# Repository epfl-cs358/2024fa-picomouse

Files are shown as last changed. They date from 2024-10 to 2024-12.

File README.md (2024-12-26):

# Picomouse

## Description
 
This project aims to create from scratch a micromouse and be able to run it on a 10x10 maze. The design of the mouse, the choice of components, the implementation of the code and the construction of the maze are parts of the project. Our team was responsible of the walls and pillars and another team had to construct the floor. The purpose of this project is to discover how to combine hardware and software and to learn how to work in a team of 6 persons.

## Table of Contents
1. [Description](#description)
2. [Mouse Components](#mouse-components)
3. [Mouse Preparation](#mouse-preparation)
4. [Mouse Assembly](#assembling-the-mouse)
5. [Maze](#maze)
6. [Software Overview](#software-overview)
7. [Software Installation](#software-installation)
8. [Sensors calibration](#sensors-calibration)
9. [Distance calculation](#distance-calculation)
10. [Computation distances with encoders](#computation-distances-with-encoders)
11. [What does the mouse?](#what-does-the-mouse)
12. [Improvements](#improvements)

## Mouse Components:
- 2 x N20 600rpm dc brushed motors
- MX1508 motor driver
- 9 volt battery
- ESP-32-vroom 32
- 5 x DFROBOT SEN0427 TOF
- DFRobot Gravity I2C BMI160 Gyroscope
- Small Bead
- M2 screws and bolts 

## Mouse Preparation:
 ### 3d Printing the components:
  The 3d files are in the CAD folder. \
  We used 10% infill for the printing. \
  1.Print the base plate: 
  
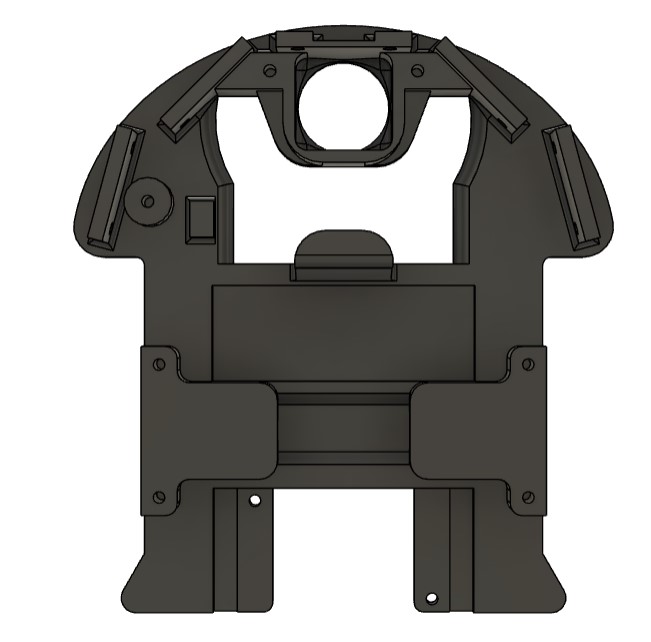
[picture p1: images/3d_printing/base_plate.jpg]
Base Plate
  
  
  2.Print the motors holders: 
  
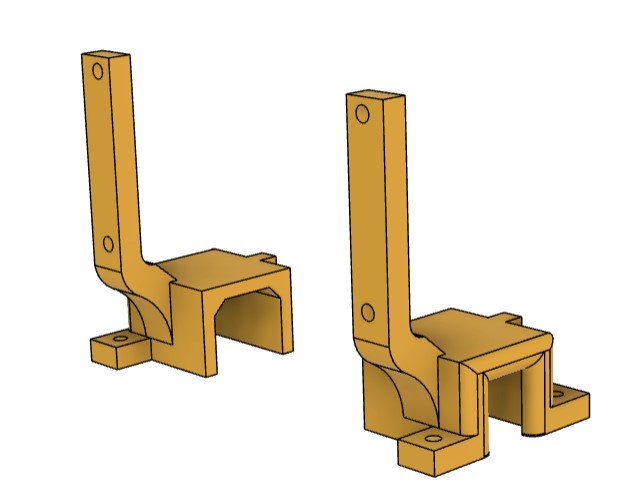
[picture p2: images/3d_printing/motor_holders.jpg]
Motor holder
   
  
  3.Print the bead holder (cap): 
  
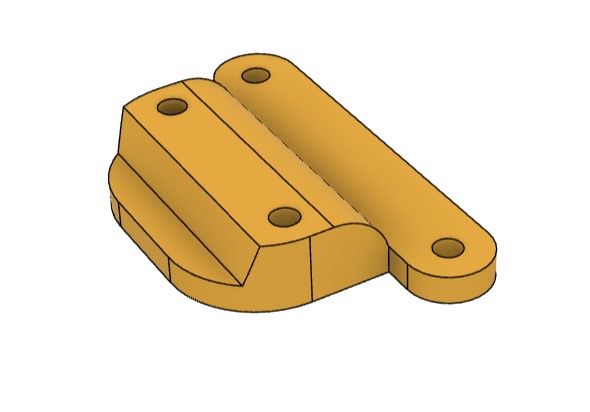
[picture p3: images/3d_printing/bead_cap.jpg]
Bead cap
   
  
  4.Print the weels: 
  The weels are composed of 2 parts: 
  - The inner wheel support printed in hard plastic (PETG/PLA). 
  - Our rubber is printed with ninjaflex TPU but elastic rubber can also be used.

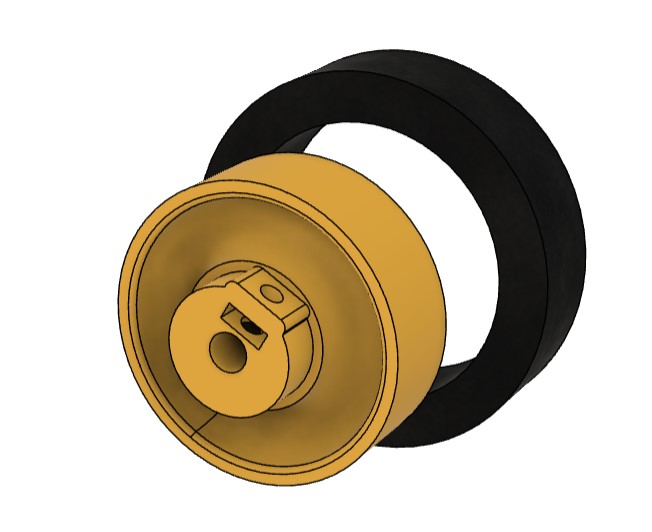
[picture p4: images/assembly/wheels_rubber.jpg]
wheels
  

## Assembling the Mouse:
  The whole mouse can be build with bolts and screws but threaded insert can be used to disassemble the mouse easily.

  #### 1.Assemble the wheels:
  Glue the rubber on the wheel. \
  Place a M2 hexnut in the dedicated slot.
  
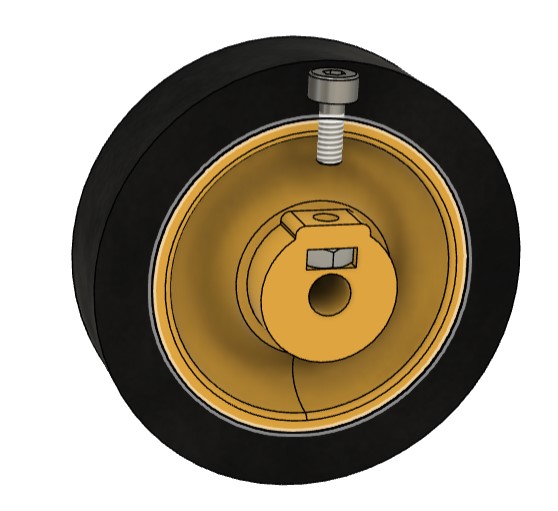
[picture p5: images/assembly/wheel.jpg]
wheels_rubber
  

  #### 2.Place and screw the buck convertor: 
    
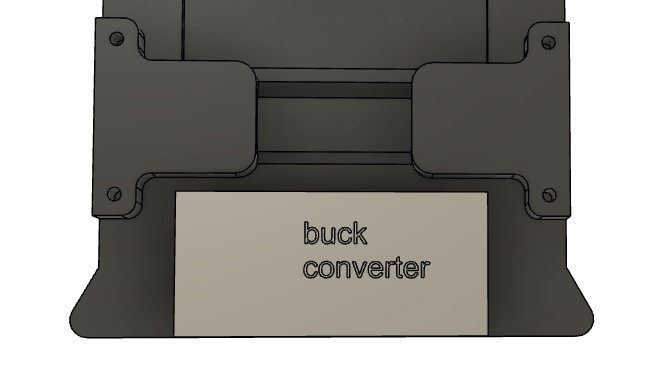
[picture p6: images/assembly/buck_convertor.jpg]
Buck convertor
   

 #### 3.Place the motors and fix them with the motors holder: 
   
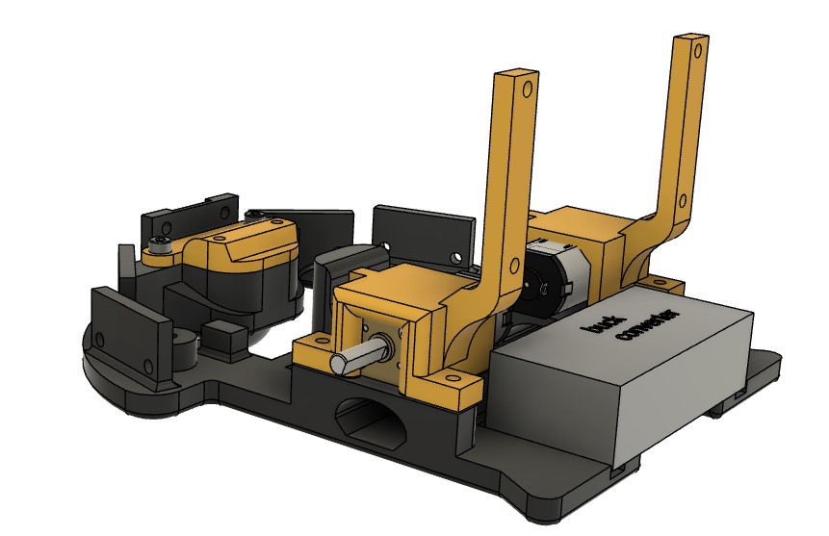
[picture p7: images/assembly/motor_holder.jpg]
Motor holder
   

 #### 4.Assemble the weels and fix them to the motor axis:

 #### 5.Place the battery: 
 
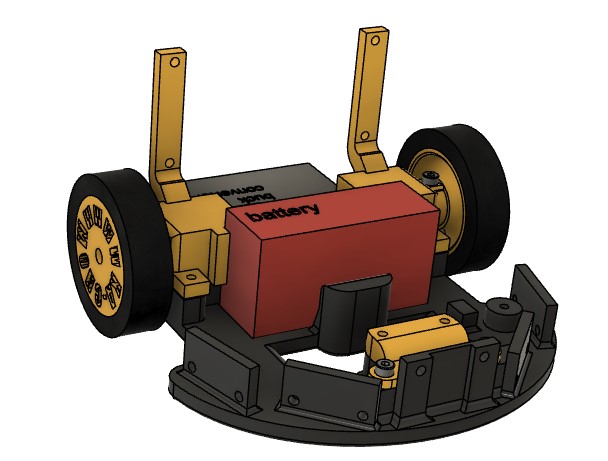
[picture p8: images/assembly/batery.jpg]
Batery
   

 #### 6.Place and screw the TOF's sensors to their dedicated slot: 
   
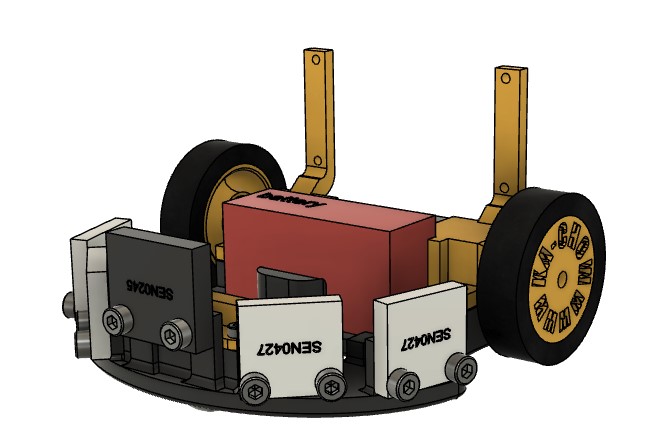
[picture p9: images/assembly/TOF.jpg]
TOF
   

 #### 7.Place and screw the gyroscope: 
  
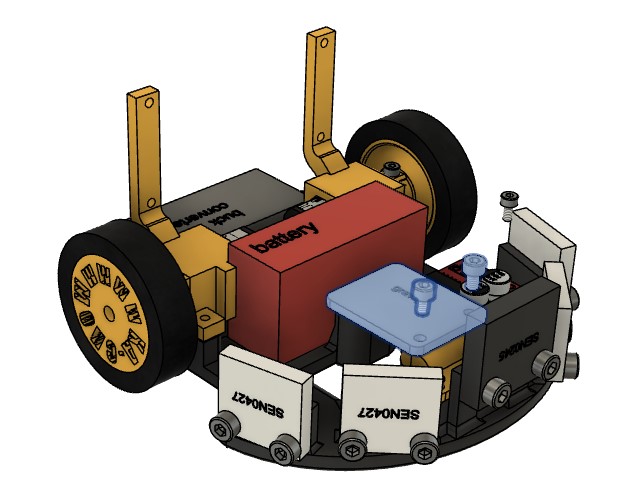
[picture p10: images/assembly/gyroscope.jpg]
   
  
  #### 8.Place and screw the ESP-32 to the back of the motor holder: 
  
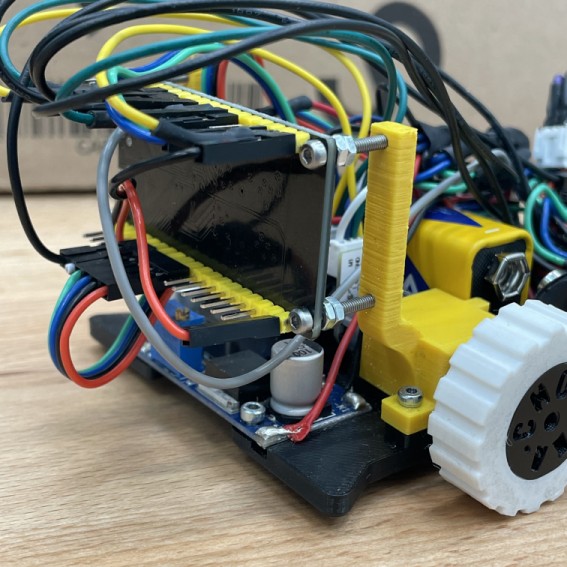
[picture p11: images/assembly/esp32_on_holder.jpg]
   
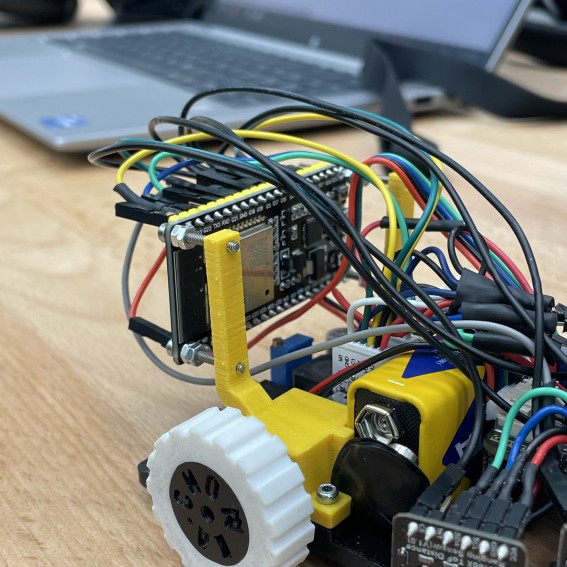
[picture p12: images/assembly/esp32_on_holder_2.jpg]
  

  ### Wiring:
  

## Maze
The competition maze is made by 18cm x 18cm cells with 2cm width walls and 16 cm x 16 cm space inside the cells.
There is also an other maze design that uses 17cm x 17cm cells with 1cm width walls. \
We decided to make the first option to align with the competition design however the second option uses less platic and wood. \
We had the constraint to make a maze that is easily dissmountable thus we used Scratch to attach the walls and the pillars to a carpet. 

### Walls:
Option1. We used 6mm and 8mm thick mdf plates. \
    See the CAD for the dimension of the cut, we used a C02 laser cutter. \
    The wall is composed of 2 plates of 16cm x 5cm and 2 dowel of 2.5cm x 4.5cm that need to be glued together. 

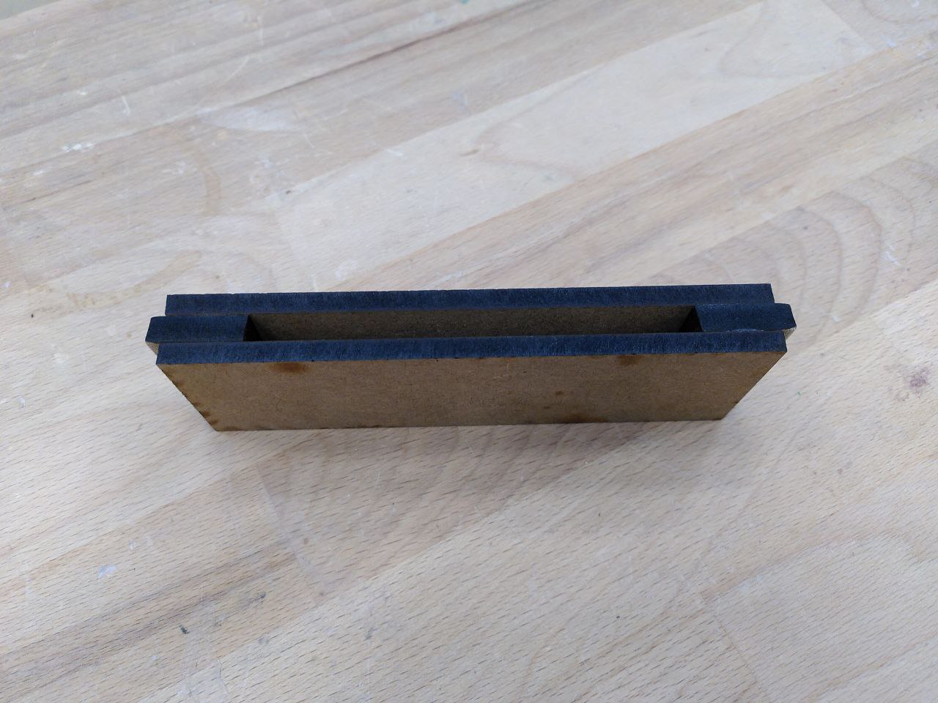
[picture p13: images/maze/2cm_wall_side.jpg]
walls2cm
 

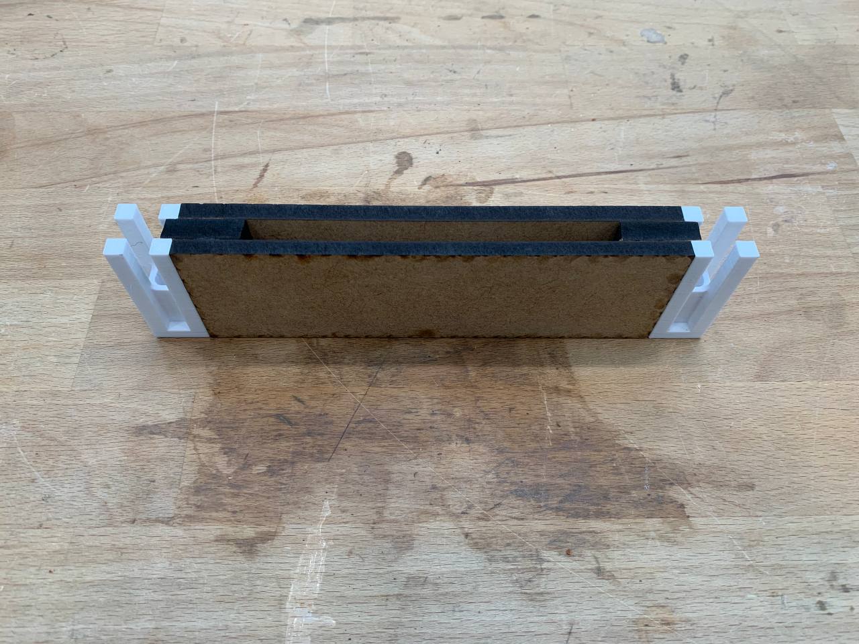
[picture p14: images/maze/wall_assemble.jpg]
walls2
     

Option2. Same as option 1 but with 3mm and 4mm thick mdf plates. \
We get the following wall:

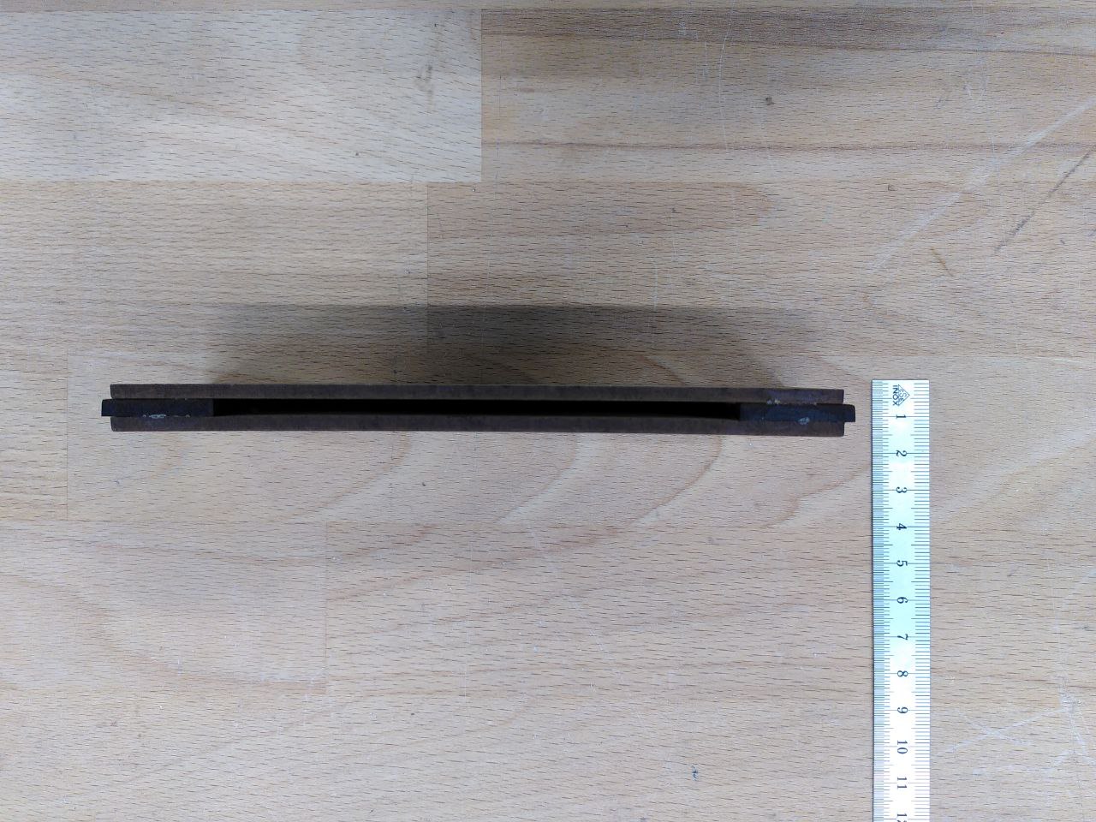
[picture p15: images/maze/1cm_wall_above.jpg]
wall1cm
 

### Pillars:
Option1. 3d print the 2cm x 2cm x 5cm pillars \

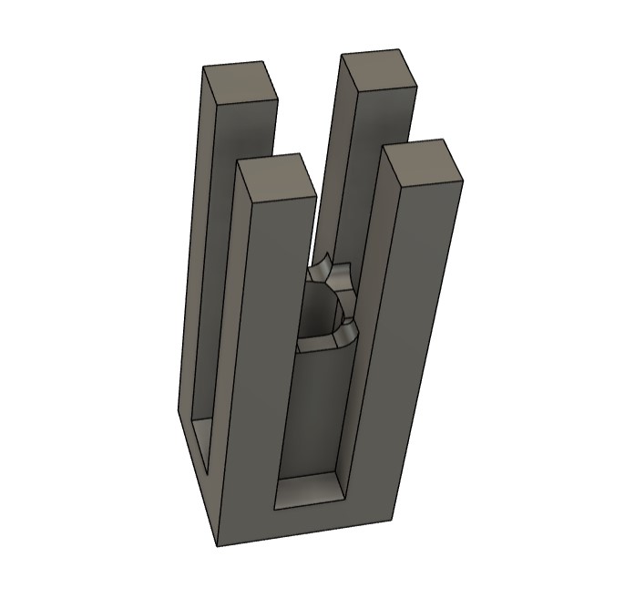
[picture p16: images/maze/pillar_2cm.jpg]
pillar_2
 

Option2. 3d print the 1cm x 1cm x 5cm pillars \

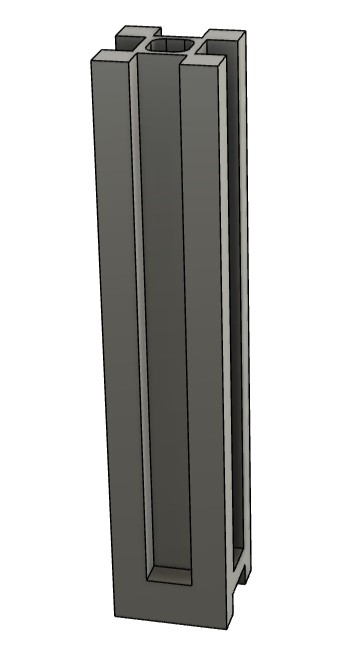
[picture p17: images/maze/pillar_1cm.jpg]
pillar_1
 
    
Both of them have an option to add a M2 hexnut inside so the pillars can be screwed underneath.\
The bolt can easily be placed using a screwdriver by pushing the bolt until you hear a pop for the 2cm x 2cm pillar. \
For the 1cm x 1cm pillar the bolt has to be glued underneath. \
The bolt should be locked in place. 

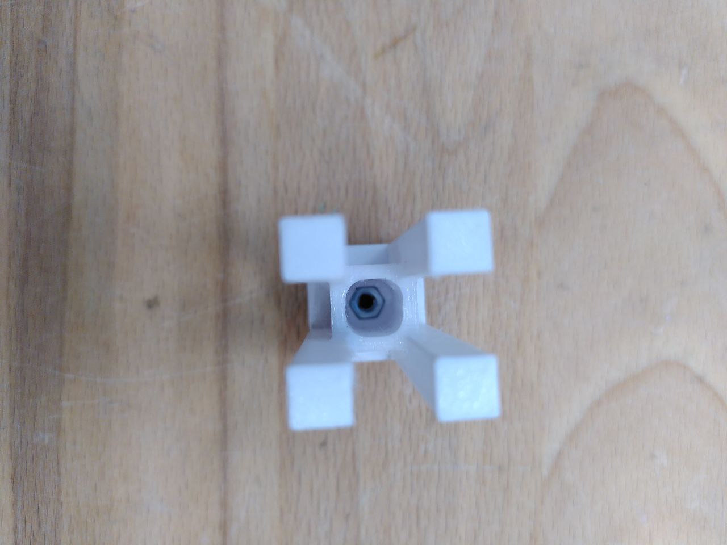
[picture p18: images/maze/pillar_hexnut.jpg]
pillar_hexnut
 

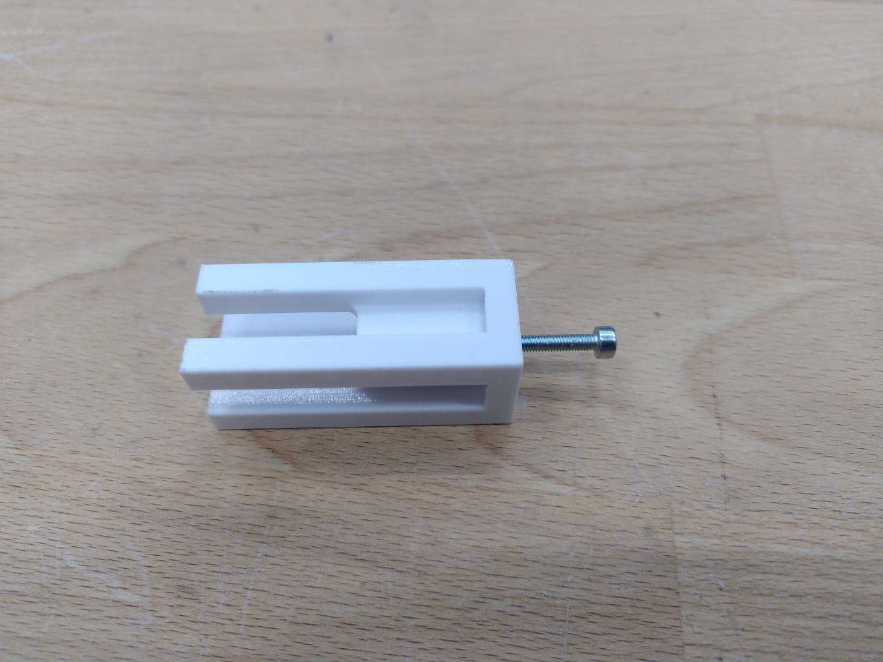
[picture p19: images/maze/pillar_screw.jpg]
pillar_screw
 

## Software Overview
### Code interface
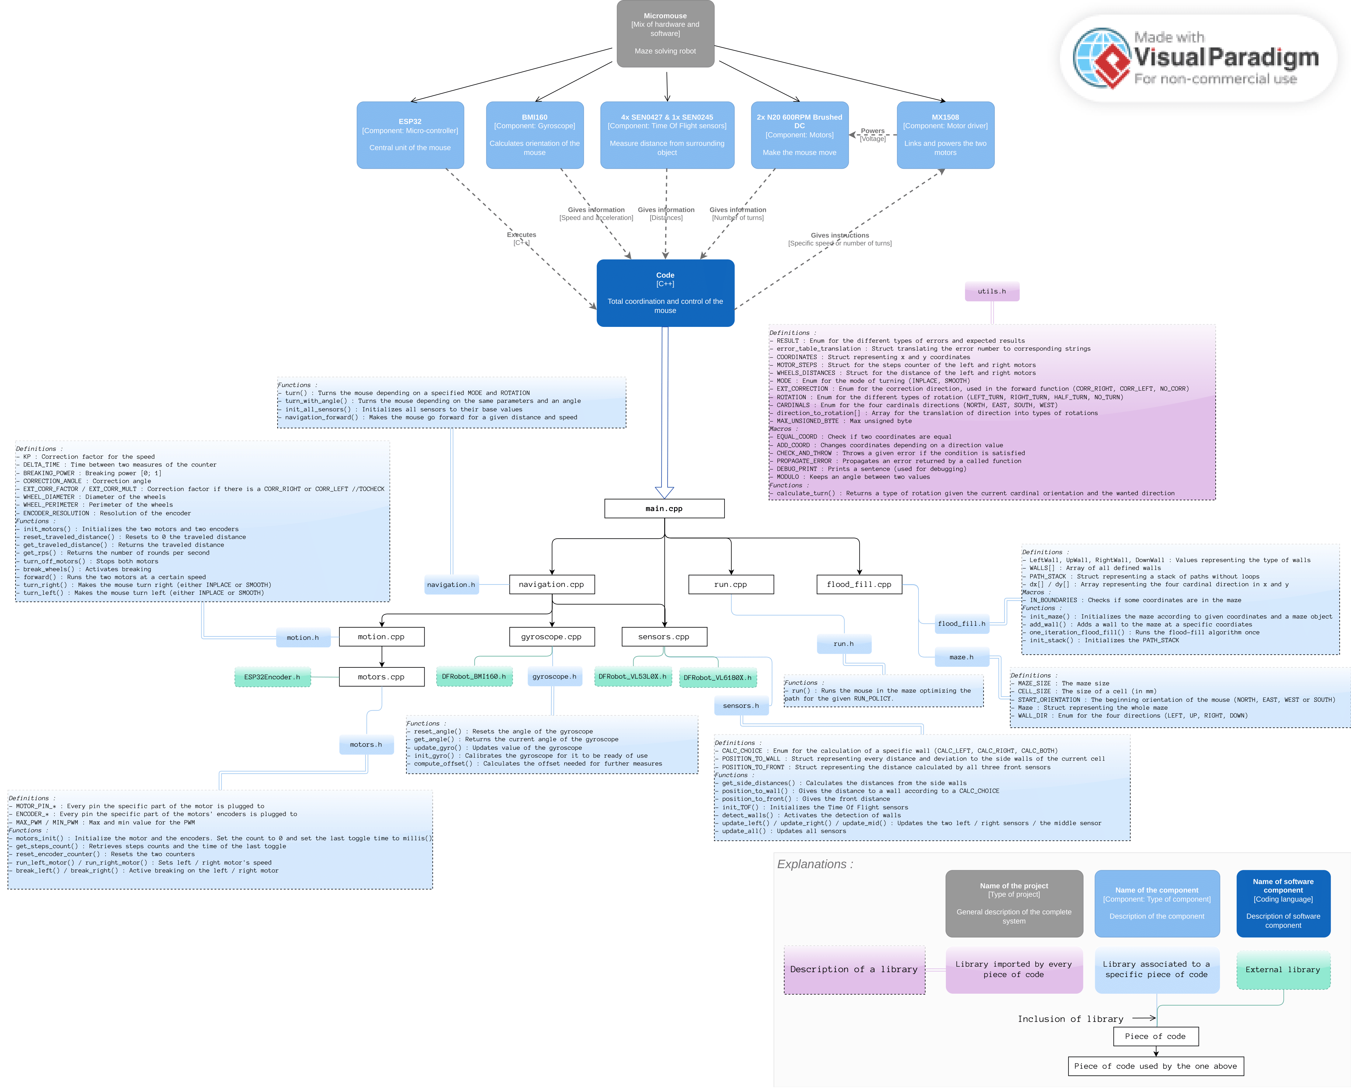
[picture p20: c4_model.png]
here
You can find a detailed scheme representing the relations of all components and pieces of code  (in .png) and here (in .pdf).
## Software Installation
  ### Software Prerequisites:
  
  - Arduino IDE
  - Python 3.10
  - Python libraries: (bleak, pygame)

### Installation:

1. Clone the repository to your local machine:
   ```bash
   git clone https://github.com/epfl-cs358/2024fa-picomouse.git
   cd 2024fa-picomouse
   ```

## Sensors calibration:
  ### TOF calibration:
  The Tof sensors need to be calibrated individually, to do that we measured different distances for each sensors and did a linear regression on the measurement     given the actual distance. \
  For our sensors we get the following graphs: \
  Where the x axis denotes the real distance and the y axis denotes the measured value. \
  The green line represent the expected slope, and the black line represent the measurements. 

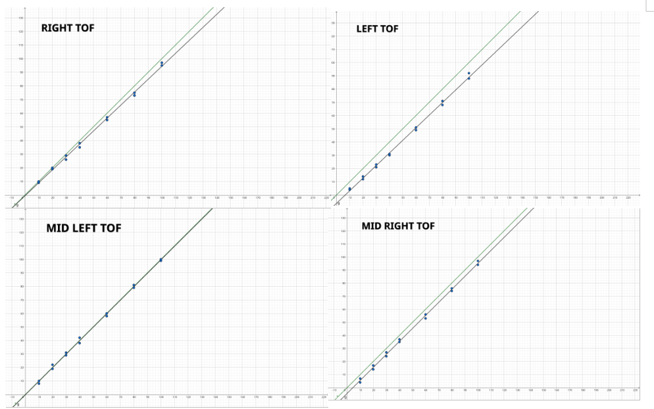
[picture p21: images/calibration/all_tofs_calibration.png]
all TOFs
  

  We get 5 slopes: \
  Left_y = 0.951x - 6.273 \
  Mid_Left_y = 0.998x - 0.189 \
  Mid_y = 1.000x - 0.000\
  Mid_Right_y = 0.995x - 4.407 \
  Right_y = 0.958x - 1.176 

  The values you will get need to be changed in sensors.h, the SLOPE and OFFSET of each captors. 

  ### Gyroscope calibration:
   The bmi60 chip is knowned for it's natural drift. To counter that the mouse, at initialization, \
   read's CALIBRATION_OFFSET_NB_ITERATIONS times the gyroscope and average the values to obtain the offset.\
   The offset itself is not sufficient, we also calibrated it with an affine function.\
   The gyroscope is also measured GYRO_NB_ITERATIONS times and average it out to mitigate the noise. \
   This parameter can also be changed in gyroscope.h. \
   If required, you can add and activation threshold.

### Distance Calculation:
Using the TOF sensors we can estimate the mouse position to a left or right wall.
We can get the mouse orientation and its distance to the wall (from the center of the mouse).
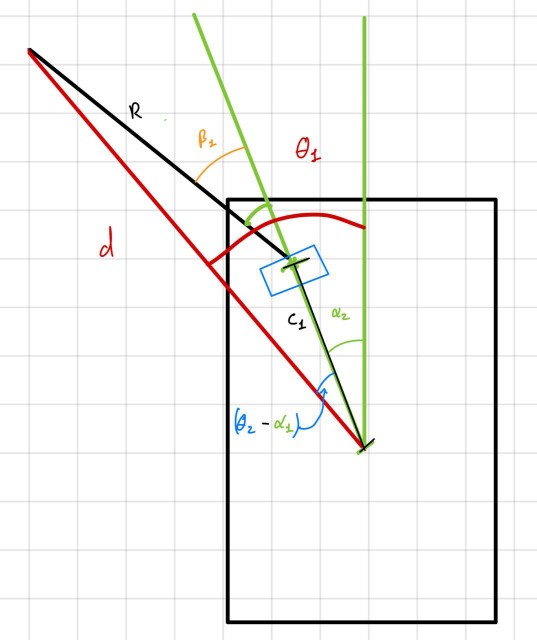
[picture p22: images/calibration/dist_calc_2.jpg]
trigo_1


$$
    \begin{aligned}
    \text{Given: } \ & \alpha_1 , \ c_1 , \ \beta_1, \ r \\
    \text{To be found: } \ & d, \ \theta_1 \\
    \newline
    d &= \sqrt{r^2 + c_1^2 - 2 \cdot r \cdot c_1 \cdot \cos(\pi - \beta_1)} \\
    \theta_1 &= \alpha_1 + \arccos\left(\frac{d^2 + c_1^2 - r^2}{2 \cdot d \cdot c_1}\right) \\
    \end{aligned}
$$

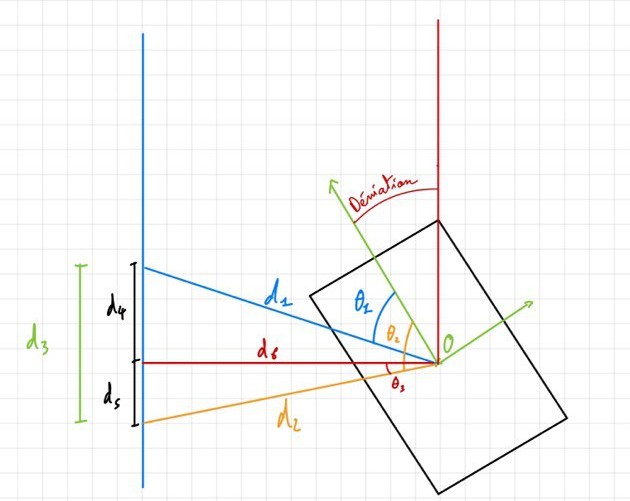
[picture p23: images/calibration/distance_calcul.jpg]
trigo_2


$$
    \begin{aligned}
    \text{Given: } \ & d_1, \ \theta_1, \ d_2, \ \theta_2 \\
    \text{To be found: } \ & d_3, \ d_5, \ d_6 \\
    \newline
    d_3 &= \sqrt{d_1^2 + d_2^2 - 2 \cdot d_1 \cdot d_2 \cdot \cos(\theta_1 - \theta_2)} \\
    d_5 &= \frac{d_2^2 + d_3^2 - d_1^2}{2 \cdot d_3} \\
    d_6 &= \sqrt{d_2^2 - d_5^2} \\
    \end{aligned}
$$

If you change the sensors disposition you need to changes those values in sensors.cpp.

## Computation distances with encoders
To compute the travel distance, one needs to know the real perimeter of the wheels and the number of pulsations transmitted by the encoder during one wheel revolution. To do that, you can modify in motion.h the constant WHEEL_DIAMETER and ENCODER_RESOLUTION.\
To compute the encoder's resolution, print get_steps_count() in a while loop and turn manually the wheel to measure the number of steps needed for one revolution.

## UI
The UI made for monitoring the mouse's position and state of the maze stored in the micro-controller is written in Python, using the [Pygame Community Edition library](https://github.com/pygame-community/pygame-ce). 
To use the provided code, you'll need to install pygame-ce (``pip install pygame-ce``) which should already be done if you installed the requirements.

### How to use
If you are simply trying to visualize the maze and play with it offline, you'll have to understand how it is interpreted by the code. Every cell is represented by a set of 4 bits. Each of these bits represents a wall. In order, the first bit represents the left wall, the second, the upper wall, the third, the right wall, the fourth, the bottom wall (i.e. 0b1010 represents a cell with a wall on the left and wall on the right).
#### Example of a complete maze
```
maze = [[0b0000, 0b0101, 0b0110, 0b1000, 0b0000, 0b0000, 0b0000, 0b0000],
        [0b1010, 0b1111, 0b1011, 0b1000, 0b0000, 0b0001, 0b0000, 0b0000],
        [0b1001, 0b0110, 0b1101, 0b0000, 0b0011, 0b1110, 0b1001, 0b0000],
        [0b0110, 0b1001, 0b0110, 0b1011, 0b1110, 0b1010, 0b1111, 0b1000],
        [0b0000, 0b0110, 0b1001, 0b0101, 0b0001, 0b0010, 0b1101, 0b0000],
        [0b0000, 0b0000, 0b0100, 0b0100, 0b0110, 0b1001, 0b0110, 0b0000],
        [0b0000, 0b0000, 0b0000, 0b0000, 0b0000, 0b0100, 0b0000, 0b0000],
        [0b0000, 0b0000, 0b0000, 0b0000, 0b0000, 0b0000, 0b0000, 0b0000]]
```
This represents the following maze :
Example UI Maze

## What does the mouse?:
The mouse navigate through the maze with the support of the gyroscope and the sensors. She does 3 runs : one to search the target cell (corner of the maze in diagonal of the start cell) by stopping in each cell, one to search a second path that could be faster than the first one when returning to the start cell, and one to run through the maze with the best path and without stopping at each cell. We use the gyroscope to keep track of and correct the current angle of the mouse in the global space. The sensors were used to detect the walls at the sides and in front of the mouse, and to recalibrate her when facing a wall.

## Improvements:
  1. Reduce the BLE (bluetooth) library so it can be compiled on the esp and used for the python script.
  2. Use a PCB as the mouse base plate to reduce the weight of the plastic plate and the cable.
  3. Make smooth turns when running the maze (after the exploration phase).
  4. Redesign of the mouse: bring closer the center of rotation to the sensors to make in place turns in less space.
  5. Better error handling for imperfect maze.
  6. Implementation of PID algorithm for sensors. The gyroscope has some limits in the precision of the turns and in straight lines, inclusion of the sensors in         the process would improve the general navigation.
  7. Ligthen weight of the mouse with a LiPo and a smaller buck converter.
  8. Usage of buck converter on motors to run at constant 6V.
  9. Redesign the floor of the maze to be more consistent (especially for the walls).
  10. Reduce the use of floating point calculations in the code using "scaled" fixed point values to improve calculation speed.

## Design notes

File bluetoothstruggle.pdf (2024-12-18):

Bluetooth struggle

This document explains why we could not finalise the UI for our project.

As part of our project, we developed a python UI which allowed us to visualise they movements of the micromouse inside the maze. The UI was implemented with Pygame, and data from micromouse was transmitted using bluetooth. For this we used the BLE library, which worked, however the big issue was the large size of the BLE library, which took around 80% of space in our ESP32. This was not usable, as the code for micromouse could not fit in the remaining 20%. We thus went on a quest to find an alternative solution. Main idea was to use a lighter bluetooth library, notably the bluetoothSerial.h, but this presented the issue of receiving the data within the pygame code.

First approach was to try to pair the esp32 with a computer directly. This did not work on Windows, we did manage to setup a bluetooth serial terminal, but we did not manage to transfer the results into the python script. Next we tried on linux, setting up the connection manually with bluetoothctl, then using command line pipelines to get the data to the python, but this approach also failed as we could not setup the bluetooth communication well.

Next idea was to use a raspberry pi. This is because raspberry pi allows you to control the GPIO pins with a python script instead of a C code like in arduino or ESP, and so we planned to import pygame in that same script and use the UI that way. We tried this by hooking up a hc05 bluetooth sensor directly to the GPIO pins of raspberry pi, but soon discovered that since raspberry has bluetooth built in, like a computer, there was not any good support for external bluetooth module. Using the built in raspberry bluetooth would be equivalent to what we tried on linux machine, so we did not attempt that. Instead we jumped through yet another loop, connecting the hc05 to arduino, arduino with a cable to raspberry, where the python code would manage the serial connection to receive bluetooth data and the pygame UI.
Picture of connection:
HC05 is connected based on the wiring to arduino, with voltage divider on its rx pin as it only accepts 3.3v logic. USB cable connects the arduino to raspbery.

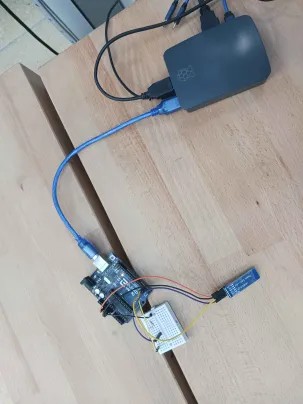
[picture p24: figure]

This finally worked. We were receiving bluetooth data sent from phone, and we had pygame running in the same script:

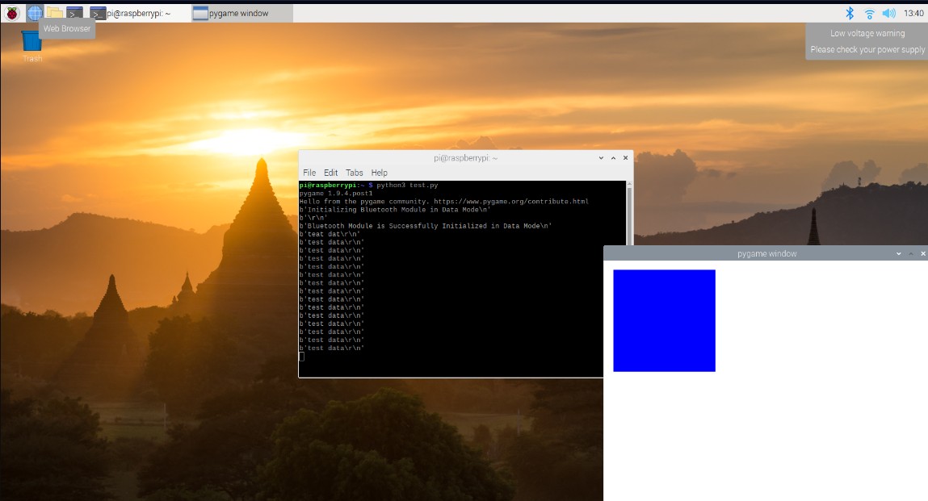
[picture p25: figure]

Code for the arduino and raspberry is also uploaded on github.
However, we ran into a last issue. Pairing the HC05 from arduino and ESP32 in micromouse ended up being more difficult than expected, and we did not manage to solve this in time to present UI in our final version of project. However we still spent a lot of time on this, and so I believe that having this document explaining the work is important.

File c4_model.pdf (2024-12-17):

### Micromouse [Mix of hardware and software]

### Maze solving robot

### ESP32 [Component: Micro-controller]

### Central unit of the mouse

### BMI160 [Component: Gyroscope]

### Calculates orientation of the mouse

### 4x SEN0427 & 1x SEN0245 [Component: Time Of Flight sensors]

### Measure distance from surrounding object

### 2x N20 600RPM Brushed

DC

### [Component: Motors]

### Make the mouse move

### Code

[C++]

### Total coordination and control of the mouse

Executes
[C++]

Gives information
[Speed and acceleration]

Gives information
[Distances]

Gives information
[Number of turns]

Gives instructions
[Specific speed or number of turns]

### main.cpp

MX1508

### [Component: Motor driver]

### Links and powers the two motors

Powers
[Voltage]

### flood_fill.cpp

flood_fill.h

Definitions :
- LeftWall, UpWall, RightWall, DownWall : Values representing the type of walls
- WALLS[] : Array of all defined walls
- PATH_STACK : Struct representing a stack of paths without loops
- dx[] / dy[] : Array representing the four cardinal direction in x and y Macros :
- IN_BOUNDARIES : Checks if some coordinates are in the maze
Functions :
- init_maze() : Initializes the maze according to given coordinates and a maze object
- add_wall() : Adds a wall to the maze at a specific coordiates
- one_iteration_flood_fill() : Runs the flood-fill algorithm once
- init_stack() : Initializes the PATH_STACK gyroscope.cpp

gyroscope.h

Functions :
- reset_angle() : Resets the angle of the gyroscope
- get_angle() : Returns the current angle of the gyroscope
- update_gyro() : Updates value of the gyroscope
- init_gyro() : Calibrates the gyroscope for it to be ready of use
- compute_offset() : Calculates the offset needed for further measures

maze.h

Definitions :
- MAZE_SIZE : The maze size
- CELL_SIZE : The size of a cell (in mm)
- START_ORIENTATION : The beginning orientation of the mouse (NORTH, EAST, WEST or SOUTH)
- Maze : Struct representing the whole maze
- WALL_DIR : Enum for the four directions (LEFT, UP, RIGHT, DOWN)
motion.h | motion.cpp

Definitions :
- KP : Correction factor for the speed
- DELTA_TIME : Time between two measures of the counter
- BREAKING_POWER : Breaking power [0; 1]
- CORRECTION_ANGLE : Correction angle
- EXT_CORR_FACTOR / EXT_CORR_MULT : Correction factor if there is a CORR_RIGHT or CORR_LEFT //TOCHECK
- WHEEL_DIAMETER : Diameter of the wheels
- WHEEL_PERIMETER : Perimeter of the wheels
- ENCODER_RESOLUTION : Resolution of the encoder
Functions :
- init_motors() : Initializes the two motors and two encoders
- reset_traveled_distance() : Resets to 0 the traveled distance
- get_traveled_distance() : Returns the traveled distance
- get_rps() : Returns the number of rounds per second
- turn_off_motors() : Stops both motors
- break_wheels() : Activates breaking
- forward() : Runs the two motors at a certain speed
- turn_right() : Makes the mouse turn right (either INPLACE or SMOOTH)
- turn_left() : Makes the mouse turn left (either INPLACE or SMOOTH)

### motors.cpp

motors.h

Definitions :
- MOTOR_PIN_* : Every pin the specific part of the motor is plugged to
- ENCODER_* : Every pin the specific part of the motors' encoders is plugged to
- MAX_PWM / MIN_PWM : Max and min value for the PWM
Functions :
- motors_init() : Initialize the motor and the encoders. Set the count to 0 and set the last toggle time to millis()
- get_steps_count() : Retrieves steps counts and the time of the last toggle
- reset_encoder_counter() : Resets the two counters
- run_left_motor() / run_right_motor() : Sets left / right motor's speed
- break_left() / break_right() : Active breaking on the left / right motor
navigation.h | navigation.cpp

Functions :
- turn() : Turns the mouse depending on a specified MODE and ROTATION
- turn_with_angle() : Turns the mouse depending on the same parameters and an angle
- init_all_sensors() : Initializes all sensors to their base values
- navigation_forward() : Makes the mouse go forward for a given distance and speed

### sensors.cpp

sensors.h

Definitions :
- CALC_CHOICE : Enum for the calculation of a specific wall (CALC_LEFT, CALC_RIGHT, CALC_BOTH)
- POSITION_TO_WALL : Struct representing every distance and deviation to the side walls of the current cell
- POSITION_TO_FRONT : Struct representing the distance calculated by all three front sensors
Functions :
- get_side_distances() : Calculates the distances from the side walls
- position_to_wall() : Gives the distance to a wall according to a CALC_CHOICE
- position_to_front() : Gives the front distance
- init_TOF() : Initializes the Time Of Flight sensors
- detect_walls() : Activates the detection of walls
- update_left() / update_right() / update_mid() : Updates the two left / right sensors / the middle sensor
- update_all() : Updates all sensors

utils.h

Definitions :
- RESULT : Enum for the different types of errors and expected results
- error_table_translation : Struct translating the error number to corresponding strings
- COORDINATES : Struct representing x and y coordinates
- MOTOR_STEPS : Struct for the steps counter of the left and right motors
- WHEELS_DISTANCES : Struct for the distance of the left and right motors
- MODE : Enum for the mode of turning (INPLACE, SMOOTH)
- EXT_CORRECTION : Enum for the correction direction, used in the forward function (CORR_RIGHT, CORR_LEFT, NO_CORR)
- ROTATION : Enum for the different types of rotation (LEFT_TURN, RIGHT_TURN, HALF_TURN, NO_TURN)
- CARDINALS : Enum for the four cardinals directions (NORTH, EAST, SOUTH, WEST)
- direction_to_rotation[] : Array for the translation of direction into types of rotations
- MAX_UNSIGNED_BYTE : Max unsigned byte
Macros :
- EQUAL_COORD : Check if two coordinates are equal
- ADD_COORD : Changes coordinates depending on a direction value
- CHECK_AND_THROW : Throws a given error if the condition is satisfied
- PROPAGATE_ERROR : Propagates an error returned by a called function
- DEBUG_PRINT : Prints a sentence (used for debugging)
- MODULO : Keeps an angle between two values
Functions :
- calculate_turn() : Returns a type of rotation given the current cardinal orientation and the wanted direction
DFRobot_BMI160.h | DFRobot_VL53L0X.h | DFRobot_VL6180X.h

### Library imported by every piece of code

### Library associated to a specific piece of code

### External library

ESP32Encoder.h

### Name of the project [Type of project]

### General description of the complete system

### Name of the component [Component: Type of component]

### Description of the component

### Name of software component [Coding language]

### Description of software component

### Piece of code

## Inclusion of library

## Description of a library

### Piece of code used by the one above

# Explanations :

### run.cpp

run.h

Functions :
- run() : Runs the mouse in the maze optimizing the path for the given RUN_POLICY.

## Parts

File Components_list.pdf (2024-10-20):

Component | Price (unit) | Quantity | Subtotal | Link
DFROBOT SEN0245 | 12,14 | 1 | 12,14 | farnell (https://ch.farnell.com/fr-CH/dfrobot/sen0245/t-l-m-tre-laser-tof-carte-arduino/dp/3517942)
DFROBOT SEN0427 | 6,79 | 4 | 27,16 | farnell (https://ch.farnell.com/fr-CH/dfrobot/sen0427/capteur-de-distance-tof-carte/dp/3879723)
Pneus Kyosho High Grip MZW2-30 | 14,70 | 1 | 14,7 | digitec (https://www.digitec.ch/fr/s1/product/kyosho-pneu-a-haute-adherence-voiture-rc-accessoires-301478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)
Athlonix 16DCT 26G1 213P.1 | 64,30 | 2 | 128,6 | digikey (https://www.digikey.ch/en/products/detail/portescap/7011906783/13997300)
Firebeetle 2 esp32-e (n16r2) | 11,88 | 1 | 11,88 | digikey (https://www.digikey.ch/fr/products/detail/dfrobot/DFR1139/24344257)
DFRobot Gravity I2C BMI160 | 8,99 | 1 | 8,99 | digikey (https://www.digikey.ch/fr/products/detail/dfrobot/SEN0250/9356335)
Engrenage plastique 35 dents | 1,33 | 4 | 5,32 | nozag (https://shop.nozag.ch/index.php?cl=details&anid=5637436870&lang=2&force_sid=7oqkh29dq7mfk0eomqr0sg3t7i)
Engrenage laiton 15 dents | 7,75 | 2 | 15,5 | nozag (https://shop.nozag.ch/index.php?cl=details&anid=5637438735&lang=2&force_sid=7oqkh29dq7mfk0eomqr0sg3t7i)
Motor controller MX1508 | 5 | 1 | 5 | Provided in the handbook
2S 7.4V 1000 mAh LiPo | 11 | 1 | 11 | Provided in the handbook
7.4 V 350 mAh LiPo | 6,75 | 1 | 6,75 | conrad (https://www.conrad.ch/fr/p/reely-pack-de-batterie-lipo-7-4-v-350-mah-nombre-de-cellules-2-25-c-softcase-bec-2617149.html)
TOTAL: | | | 247,04

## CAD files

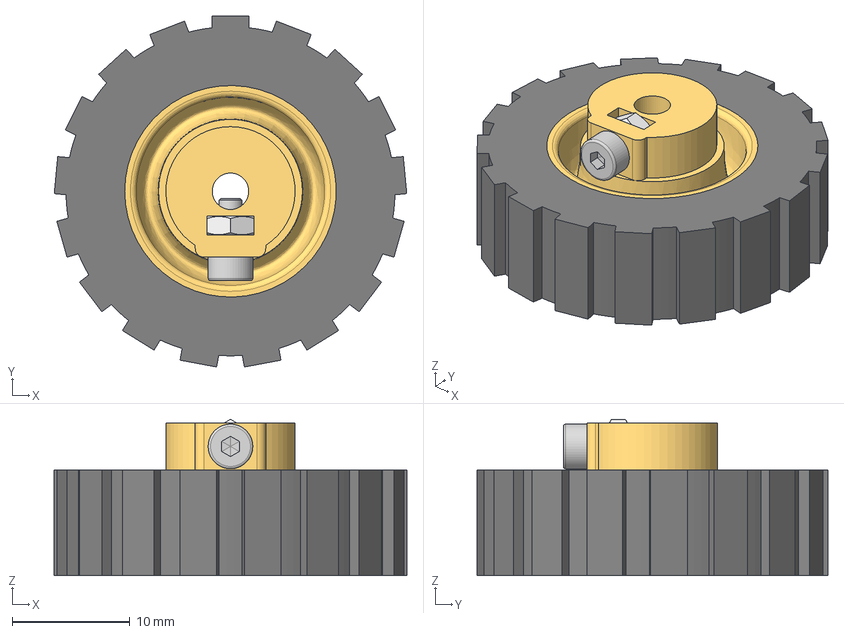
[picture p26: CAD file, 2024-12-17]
CAD/rim V3 v12.step
30.0 x 29.9 x 13.3 mm

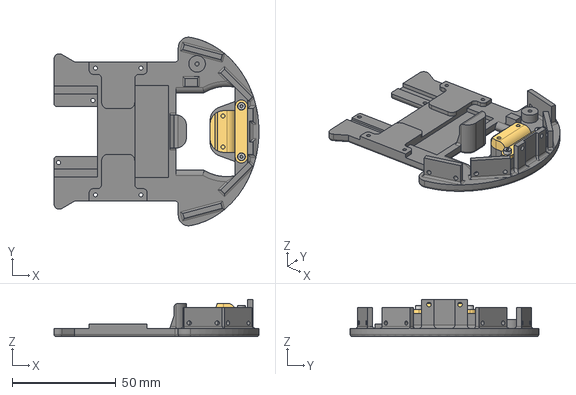
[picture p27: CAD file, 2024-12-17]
CAD/frame V3 v39.step
99.0 x 91.1 x 18.0 mm

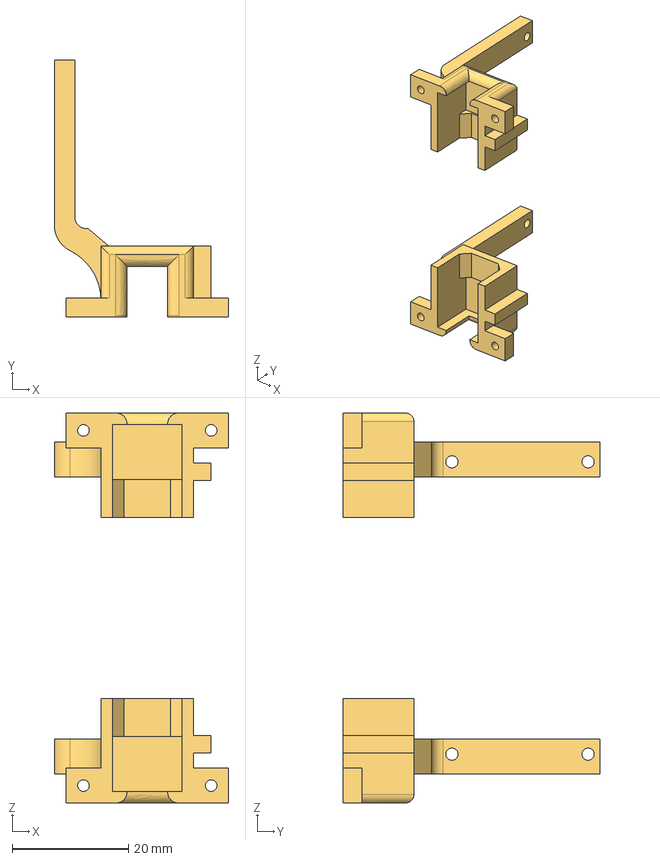
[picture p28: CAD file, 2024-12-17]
CAD/Motor holder V3 v38.step
30.0 x 44.2 x 67.2 mm

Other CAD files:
CAD/Pillar 2cm_.f3d
CAD/pillar 1cm.f3d
CAD/pillar_1cm_without_bolt.f3d

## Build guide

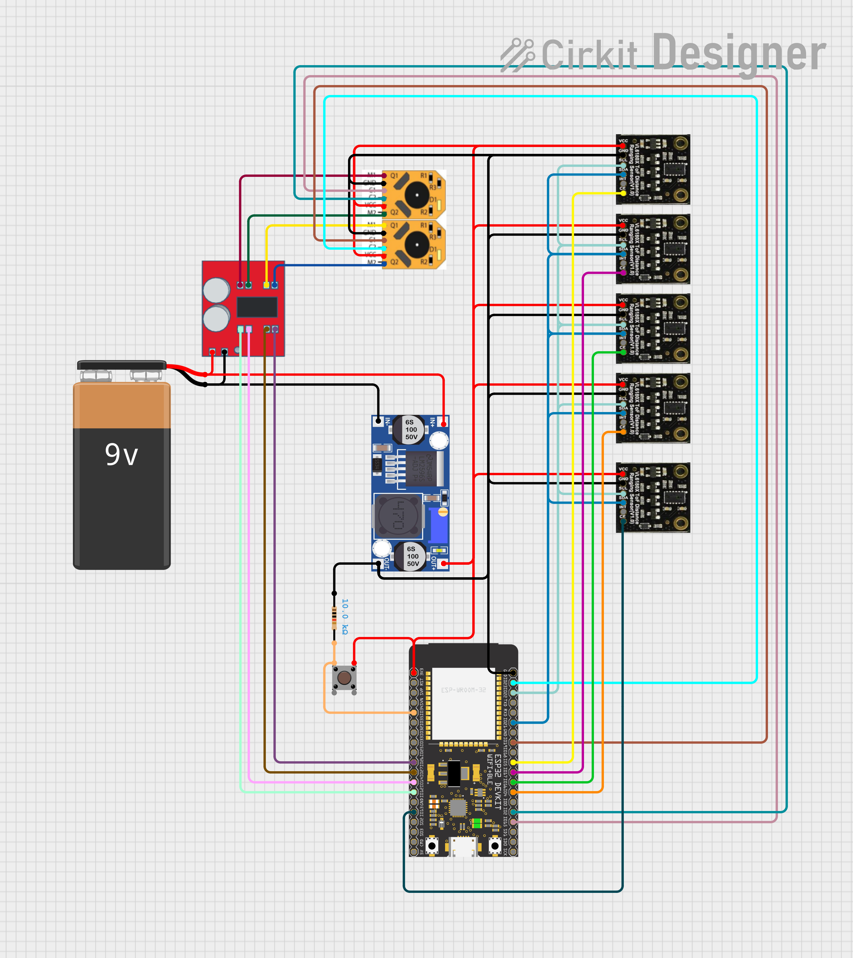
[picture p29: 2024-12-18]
images/assembly/circuit_image (4).png

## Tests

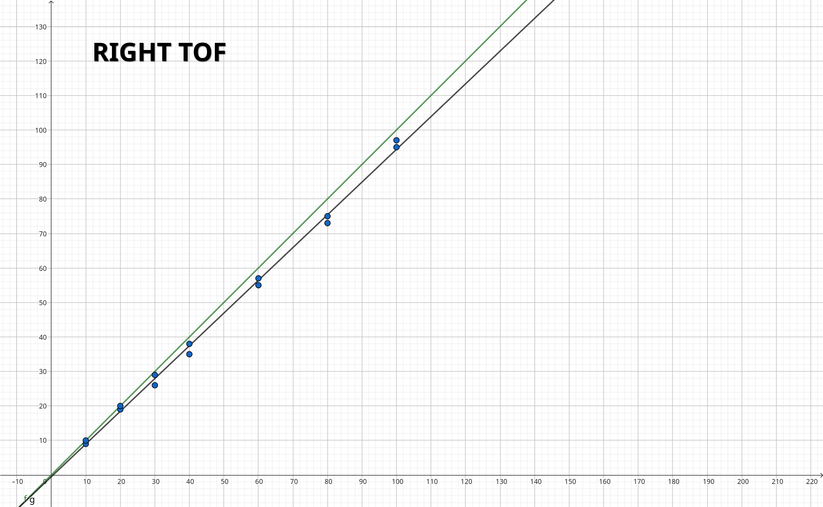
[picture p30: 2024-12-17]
images/calibration/right_captor_calibration.png

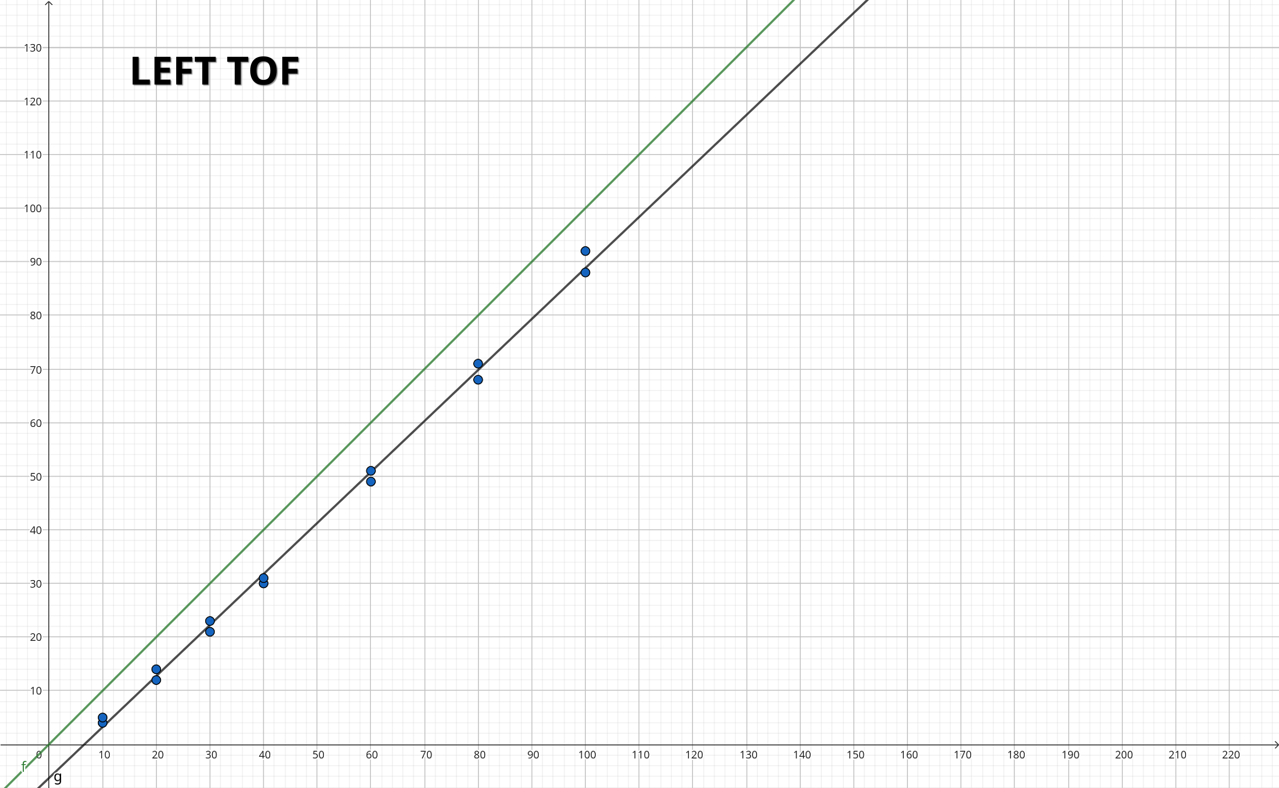
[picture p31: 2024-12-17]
images/calibration/left_captor_calibration.png

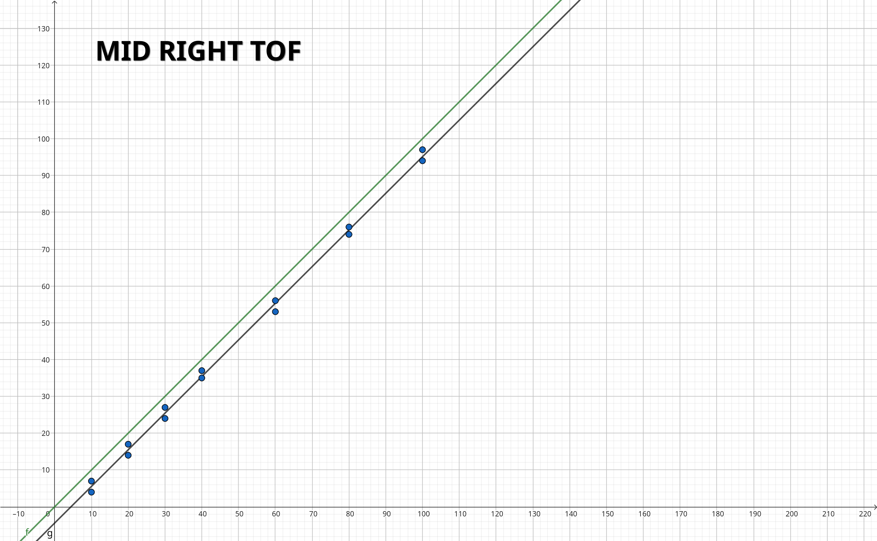
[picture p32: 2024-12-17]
images/calibration/mid_right_captor_calibration.png

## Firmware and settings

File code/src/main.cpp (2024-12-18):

#include "flood_fill.h"
#include "gyroscope.h"
#include "maze.h"
#include "motion.h"
#include "navigation.h"
#include "run.h"
#include "sensors.h"
#include "utils.h"
#include <Wire.h>
#include <cmath>
#include <math.h>

#define BUTTON_PIN 34

#define CELL_LENGTH 180  // in mm

// Defined speeds for both run and search mode
#define MAX_SPEED_SEARCH 0.08
#define MAX_SPEED_RUN 0.16

#define NB_TOF_SAMPLE 2

int run1 = 1;
int run2 = 0;
int final_run = 1;
int end = 0;
int button_state = 0;
Maze maze;
COORDINATES start_cell = { 0, 0 };
COORDINATES exit_cell = { MAZE_SIZE - 1, MAZE_SIZE - 1 };
PATH_STACK path_run1;
PATH_STACK path_run2;

CARDINALS current_direction;

#define BLOCK_ON_ERROR(error, message) \
  while (error) { \
    message; \
    Serial.printf("Error: %s \n", error_table_translation[error]); \
    delay(1000); \
  }

RESULT correct_direction(CALC_CHOICE choice);



void setup() {
  Serial.begin(115200);
  delay(20);
  Wire.begin();
  delay(20);
  pinMode(BUTTON_PIN, INPUT);
  delay(5000);
  RESULT err = init_all_sensors();

  BLOCK_ON_ERROR(err, Serial.println("Error occured in initialization."));

  err = init_maze(&maze, start_cell, exit_cell);
  Serial.printf("mouse x : %d, mouse y : %d, end x: %d, end y : %d \n",
                maze.mouse_pos.x, maze.mouse_pos.y, maze.exit.x, maze.exit.y);
  BLOCK_ON_ERROR(
    err,
    Serial.println("Btw you need to give valid start and exit coordinates"));

  err = init_stack(&path_run1);
  BLOCK_ON_ERROR(err, Serial.println("Stack failed."));
  err = init_stack(&path_run2);
  BLOCK_ON_ERROR(err, Serial.println("Stack failed."));

  current_direction = START_ORIENTATION;
}

void loop() {
  if (run1) {
    Serial.println("code started");
    // TODO peut etre qu'il faut update le gyro plus que ça
    WALL_DIR new_walls[3];
    int len = 0;
    CARDINALS next_direction;
    RESULT rslt = detect_walls(new_walls, &len, current_direction);

    BLOCK_ON_ERROR(rslt, Serial.println("wall detection failed !!"));
    // TODO: check rslt
    for (int i = 0; i < len; i++) {
      Serial.println(new_walls[i]);
      rslt = add_wall(&maze, new_walls[i]);
      BLOCK_ON_ERROR(rslt, Serial.println("add wall failed !!"));
    }
    Serial.println("add walls done");

    rslt = one_iteration_flood_fill(&maze, &path_run1, &next_direction);
    Serial.println("flood fill done");
    Serial.println(rslt);

    // BLOCK_ON_ERROR(rslt && rslt != MOUSE_END, Serial.println("flood fill
    // failed !!"));

    if (rslt != MOUSE_END) {
      Serial.println(next_direction);
      ROTATION rotation = calculate_turn(current_direction, next_direction);

      current_direction = next_direction;

      if (rotation == NO_TURN) {
        rslt = correct_direction(CALC_BOTH);
      }
      if (rslt == CANNOT_CORRECT || rotation != NO_TURN) {

        rslt = turn(rotation, INPLACE);
        BLOCK_ON_ERROR(rslt, Serial.println("turn failed !!"));
        // TODO: check rslt
        delay(10);
        rslt = navigation_forward(CELL_LENGTH, MAX_SPEED_SEARCH);
        BLOCK_ON_ERROR(rslt, Serial.println("navigation forward failed !!"));
        // TODO: check rslt
      }
    } else {
      run1 = 0;
      run2 = 1;
      maze.start = exit_cell;
      maze.exit = start_cell;
    }

  } else if (run2) {
    Serial.println("code started");

    WALL_DIR new_walls[3];
    int len = 0;
    CARDINALS next_direction;
    RESULT rslt = detect_walls(new_walls, &len, current_direction);

    BLOCK_ON_ERROR(rslt, Serial.println("wall detection failed !!"));
    // TODO: check rslt
    for (int i = 0; i < len; i++) {
      Serial.println(new_walls[i]);
      rslt = add_wall(&maze, new_walls[i]);
      BLOCK_ON_ERROR(rslt, Serial.println("add wall failed !!"));
    }
    Serial.println("add walls done");

    rslt = one_iteration_flood_fill(&maze, &path_run2, &next_direction);
    Serial.println("flood fill done");
    Serial.println(rslt);

    // BLOCK_ON_ERROR(rslt && rslt != MOUSE_END, Serial.println("flood fill
    // failed !!"));

    if (rslt != MOUSE_END) {
      Serial.println(next_direction);
      ROTATION rotation = calculate_turn(current_direction, next_direction);

      current_direction = next_direction;


      if (rotation == NO_TURN) {
        rslt = correct_direction(CALC_BOTH);
      }
      if (rslt == CANNOT_CORRECT || rotation != NO_TURN) {

        rslt = turn(rotation, INPLACE);
        BLOCK_ON_ERROR(rslt, Serial.println("turn failed !!"));
        // TODO: check rslt
        delay(10);
        rslt = navigation_forward(CELL_LENGTH, MAX_SPEED_SEARCH);
        BLOCK_ON_ERROR(rslt, Serial.println("navigation forward failed !!"));
        // TODO: check rslt
      }
    } else {
      run2 = 0;
    }
  } else if (final_run) {
    while (button_state == LOW) {
      button_state = digitalRead(BUTTON_PIN);
      delay(100);
    }
    init_gyro();
    ROTATION rotation = calculate_turn(current_direction, START_ORIENTATION);
    RESULT rslt = turn(rotation, INPLACE);
    BLOCK_ON_ERROR(rslt, Serial.println("turn failed !!"));
    run(&path_run1, &path_run2, MAX_SPEED_RUN);
    final_run = 0;
  }

  for (int i = 0; i < 15; i++) {
    update_gyro();
  }
}


RESULT correct_direction(CALC_CHOICE choice) {
  POSITION_TO_WALL tof_dist;

  float dist_L = 0;
  float dist_R = 0;

  for (int i = 0; i < NB_TOF_SAMPLE;i++) {
    RESULT rslt = position_to_wall(&tof_dist, choice);
    PROPAGATE_ERROR(rslt);
    dist_L += tof_dist.distance_left;
    dist_R += tof_dist.distance_right;
    delay(2);
  }
  dist_L /= NB_TOF_SAMPLE;
  dist_R /= NB_TOF_SAMPLE;

  float total_dist = dist_L + dist_R;
  float dist;
  float angle;

  if (total_dist > 155 && total_dist < 165) {
    // We trust the sensors
    float error = (dist_L - dist_R) / 2;

    angle = error > 0 ? 1 : -1;
    angle *= 0.5 - atan(CELL_SIZE / fabs(error)) / M_PI;

    dist = sqrt(pow(fabs(error), 2) + pow(CELL_SIZE, 2));

  } /**else if (dist_L < 55) {
    float error = (dist_L / 2);

    angle = -(0.5 - atan(CELL_SIZE / error) / M_PI);
    dist = sqrt(pow(fabs(error), 2) + pow(CELL_SIZE, 2));

  } else if (dist_R < 55) {
    float error = (dist_R / 2);

    angle = 0.5 - atan(CELL_SIZE / (error)) / M_PI;
    dist = sqrt(pow(fabs(error), 2) + pow(CELL_SIZE, 2));
  } */else {
    return CANNOT_CORRECT;
  }

  DEBBUG_PRINT(Serial.print("distance     "); Serial.println(dist););

  turn_with_angle(angle, INPLACE);
  navigation_forward(dist, MAX_SPEED_SEARCH);
  update_gyro();
  turn_with_angle(-angle, INPLACE);
  return NO_ERROR;
}

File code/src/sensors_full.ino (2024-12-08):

#include "sensors.h"
#include <Wire.h>

void setup(){
  Serial.begin(115200);
  delay(100);
  Wire.begin();
  delay(100);
  Serial.println("ff irl ");
  RESULT res = init_TOF();
  Serial.println(res);


}
uint16_t distances[4];

void loop(){
  RESULT res = update_all();
  Serial.println(res);
  ///CHECK_AND_THROW(!sensor.begin(), TOF_INIT_FAIL);
  get_side_side_distances(distances);
  Serial.printf("left: %hu mid_left: %hu  mid_right: %hu  right: %hu \n", distances[0],  distances[1], distances[2],  distances[3]);
  delay(500);
}

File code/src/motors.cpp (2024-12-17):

/**
 * @file motion.cpp
 * @author PEREGO Zac 
 * @copyright Copyright (c) 2024
 */

#include "motors.h"
#include "math.h"
#include "utils.h"
#include <ESP32Encoder.h>
#include <Arduino.h>

bool motorR_running;
bool motorL_running;

// Encoder object for the two motors
ESP32Encoder encoderL;
ESP32Encoder encoderR;

// =========== Private functions ===========
/**
 * @brief Run the given motor at a certain speed
 * @param int PWM The speed of the motor
 * @param bool right_motor True if the motor is the right one
 * @return None
 */
void run_motor(int PWM, bool right_motor, bool forward)
{
	int pin1;
	int pin2;

	// Set the pins
	if (right_motor)
	{
		pin1 = MOTOR_PIN_R1;
		pin2 = MOTOR_PIN_R2;
	}
	else
	{
		pin1 = MOTOR_PIN_L1;
		pin2 = MOTOR_PIN_L2;
	}

	// Apply the PWM with the right direction
	if (forward)
	{
		analogWrite(pin1, PWM);
		analogWrite(pin2, LOW);
	}
	else
	{
		analogWrite(pin1, LOW);
		analogWrite(pin2, PWM);
	}
}

/**
 * @brief take the desired speed and convert it to a PWM value
 *
 * @param float speed The speed about to be scaled
 * @return the PWM value
 */
int speed_to_pwm(float speed)
{
	if (fabs(speed) < 0.0000000000000001)
	{
		return 0;
	}

	// Calculate the PWM
	int PWM = (int)(MIN_PWM + fabs(speed) * (MAX_PWM - MIN_PWM));
	return PWM;
}

// =========== Public functions ===========

RESULT motors_init()
{
	// ---- Setup motor -----

	motorR_running = false;
	motorL_running = false;

	// Set the pins as output
	pinMode(MOTOR_PIN_R1, OUTPUT);
	pinMode(MOTOR_PIN_R2, OUTPUT);
	pinMode(MOTOR_PIN_L1, OUTPUT);
	pinMode(MOTOR_PIN_L2, OUTPUT);

	// ----- Setup encoder ----
	// Enable the weak pull up resistors
	ESP32Encoder::useInternalWeakPullResistors = puType::up;

	// Attach the encoders to the pins
	// 4 count per rotation
	encoderL.attachHalfQuad(ENCODER_L1, ENCODER_L2);
	encoderR.attachHalfQuad(ENCODER_R1, ENCODER_R2);

	// Set the initial count to 0
	encoderL.clearCount();
	encoderR.clearCount();
	encoderL.setCount(100000);
	encoderR.setCount(100000);

	return NO_ERROR;
}

MOTOR_STEPS get_steps_count()
{
	// Counters for steps of the two motors
	MOTOR_STEPS motor_steps;

	motor_steps.left_count = encoderL.getCount();
	motor_steps.right_count = encoderR.getCount();

	return motor_steps;
}

RESULT reset_encoder_counter()
{
DEBBUG_PRINT(
	Serial.print("count:");\
	Serial.print(encoderL.getCount());\
	Serial.print("    ");\
	Serial.println(encoderR.getCount());
	);
    
	encoderL.clearCount();
	encoderR.clearCount();
	return NO_ERROR;
}

RESULT run_left_motor(float speed)
{
	motorL_running = true;
	if (speed == 0)
	{
		motorL_running = false;
	}
	// define the direction of the motor
	bool forward = (speed >= 0);
	speed = fabs(speed);

	int PWM = speed_to_pwm(speed);
	run_motor(PWM, false, forward);
	return NO_ERROR;
}

RESULT run_right_motor(float speed)
{
	motorR_running = true;
	if (speed == 0)
	{
		motorR_running = false;
	}
	// define the direction of the motor
	bool forward = (speed >= 0);
	speed = fabs(speed);

	int PWM = speed_to_pwm(speed);
	run_motor(PWM, true, forward);
	return NO_ERROR;
}

RESULT break_left(float breaking_power)
{
	breaking_power = fabs(breaking_power) > 1 ? 1 : fabs(breaking_power);
	int brakePWM = breaking_power * MAX_PWM;
	analogWrite(MOTOR_PIN_L1, brakePWM);
	analogWrite(MOTOR_PIN_L2, brakePWM);
	return NO_ERROR;
}

RESULT break_right(float breaking_power)
{
	breaking_power = fabs(breaking_power) > 1 ? 1 : fabs(breaking_power);
	int brakePWM = breaking_power * MAX_PWM;
	analogWrite(MOTOR_PIN_R1, brakePWM);
	analogWrite(MOTOR_PIN_R2, brakePWM);
	return NO_ERROR;
}

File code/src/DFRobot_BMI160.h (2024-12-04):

#pragma once 
/*!
 * @file DFRobot_BMI160.h
 * @brief Define the basic structure of class DFRobot_BMI160 
 * @copyright	Copyright (c) 2010 DFRobot Co.Ltd (http://www.dfrobot.com)
 * @license The MIT License (MIT)
 * @author  DFRobot_haoJ(hao.jiang@dfrobot.com)
 * @version V1.0
 * @date 2017-12-01
 * @url https://github.com/DFRobot/DFRobot_BMI160
 */

#include<Arduino.h>
#include<Wire.h>
#include<SPI.h>

#define LITTLE_ENDIAN 1

/** Mask definitions */
#define BMI160_ACCEL_BW_MASK                    UINT8_C(0x70)
#define BMI160_ACCEL_ODR_MASK                   UINT8_C(0x0F)
#define BMI160_ACCEL_UNDERSAMPLING_MASK         UINT8_C(0x80)
#define BMI160_ACCEL_RANGE_MASK                 UINT8_C(0x0F)
#define BMI160_GYRO_BW_MASK                     UINT8_C(0x30)
#define BMI160_GYRO_ODR_MASK                    UINT8_C(0x0F)
#define BMI160_GYRO_RANGE_MSK                   UINT8_C(0x07)

/** Mask definitions for INT_EN registers */
#define BMI160_ANY_MOTION_X_INT_EN_MASK         UINT8_C(0x01)
#define BMI160_HIGH_G_X_INT_EN_MASK             UINT8_C(0x01)
#define BMI160_NO_MOTION_X_INT_EN_MASK          UINT8_C(0x01)
#define BMI160_ANY_MOTION_Y_INT_EN_MASK         UINT8_C(0x02)
#define BMI160_HIGH_G_Y_INT_EN_MASK             UINT8_C(0x02)
#define BMI160_NO_MOTION_Y_INT_EN_MASK          UINT8_C(0x02)
#define BMI160_ANY_MOTION_Z_INT_EN_MASK         UINT8_C(0x04)
#define BMI160_HIGH_G_Z_INT_EN_MASK             UINT8_C(0x04)
#define BMI160_NO_MOTION_Z_INT_EN_MASK          UINT8_C(0x04)
#define BMI160_SIG_MOTION_INT_EN_MASK           UINT8_C(0x07)
#define BMI160_ANY_MOTION_ALL_INT_EN_MASK       UINT8_C(0x07)
#define BMI160_STEP_DETECT_INT_EN_MASK          UINT8_C(0x08)
#define BMI160_DOUBLE_TAP_INT_EN_MASK           UINT8_C(0x10)
#define BMI160_SINGLE_TAP_INT_EN_MASK           UINT8_C(0x20)
#define BMI160_FIFO_FULL_INT_EN_MASK            UINT8_C(0x20)
#define BMI160_ORIENT_INT_EN_MASK               UINT8_C(0x40)
#define BMI160_FIFO_WATERMARK_INT_EN_MASK       UINT8_C(0x40)
#define BMI160_LOW_G_INT_EN_MASK                UINT8_C(0x08)
#define BMI160_STEP_DETECT_EN_MASK              UINT8_C(0x08)
#define BMI160_FLAT_INT_EN_MASK                 UINT8_C(0x80)
#define BMI160_DATA_RDY_INT_EN_MASK             UINT8_C(0x10)

/** Mask definitions for INT_OUT_CTRL register */
#define BMI160_INT1_EDGE_CTRL_MASK              UINT8_C(0x01)
#define BMI160_INT1_OUTPUT_MODE_MASK            UINT8_C(0x04)
#define BMI160_INT1_OUTPUT_TYPE_MASK            UINT8_C(0x02)
#define BMI160_INT1_OUTPUT_EN_MASK              UINT8_C(0x08)
#define BMI160_INT2_EDGE_CTRL_MASK              UINT8_C(0x10)
#define BMI160_INT2_OUTPUT_MODE_MASK            UINT8_C(0x40)
#define BMI160_INT2_OUTPUT_TYPE_MASK            UINT8_C(0x20)
#define BMI160_INT2_OUTPUT_EN_MASK              UINT8_C(0x80)

/** Mask definitions for INT_LATCH register */
#define BMI160_INT1_INPUT_EN_MASK               UINT8_C(0x10)
#define BMI160_INT2_INPUT_EN_MASK               UINT8_C(0x20)
#define BMI160_INT_LATCH_MASK                   UINT8_C(0x0F)

/** Mask definitions for INT_MAP register */
#define BMI160_INT1_LOW_G_MASK                  UINT8_C(0x01)
#define BMI160_INT1_HIGH_G_MASK                 UINT8_C(0x02)
#define BMI160_INT1_SLOPE_MASK                  UINT8_C(0x04)
#define BMI160_INT1_NO_MOTION_MASK              UINT8_C(0x08)
#define BMI160_INT1_DOUBLE_TAP_MASK             UINT8_C(0x10)
#define BMI160_INT1_SINGLE_TAP_MASK             UINT8_C(0x20)
#define BMI160_INT1_FIFO_FULL_MASK              UINT8_C(0x20)
#define BMI160_INT1_FIFO_WM_MASK                UINT8_C(0x40)
#define BMI160_INT1_ORIENT_MASK                 UINT8_C(0x40)
#define BMI160_INT1_FLAT_MASK                   UINT8_C(0x80)
#define BMI160_INT1_DATA_READY_MASK             UINT8_C(0x80)
#define BMI160_INT2_LOW_G_MASK                  UINT8_C(0x01)
#define BMI160_INT1_LOW_STEP_DETECT_MASK        UINT8_C(0x01)
#define BMI160_INT2_LOW_STEP_DETECT_MASK        UINT8_C(0x01)
#define BMI160_INT2_HIGH_G_MASK                 UINT8_C(0x02)
#define BMI160_INT2_FIFO_FULL_MASK              UINT8_C(0x02)
#define BMI160_INT2_FIFO_WM_MASK    UINT8_C(0x04)
#define BMI160_INT2_SLOPE_MASK                  UINT8_C(0x04)
#define BMI160_INT2_DATA_READY_MASK             UINT8_C(0x08)
#define BMI160_INT2_NO_MOTION_MASK              UINT8_C(0x08)
#define BMI160_INT2_DOUBLE_TAP_MASK             UINT8_C(0x10)
#define BMI160_INT2_SINGLE_TAP_MASK             UINT8_C(0x20)
#define BMI160_INT2_ORIENT_MASK                 UINT8_C(0x40)
#define BMI160_INT2_FLAT_MASK                   UINT8_C(0x80)

/** Mask definitions for INT_DATA register */
#define BMI160_TAP_SRC_INT_MASK                 UINT8_C(0x08)
#define BMI160_LOW_HIGH_SRC_INT_MASK            UINT8_C(0x80)
#define BMI160_MOTION_SRC_INT_MASK              UINT8_C(0x80)

/** Mask definitions for INT_MOTION register */
#define BMI160_SLOPE_INT_DUR_MASK               UINT8_C(0x03)
#define BMI160_NO_MOTION_INT_DUR_MASK           UINT8_C(0xFC)
#define BMI160_NO_MOTION_SEL_BIT_MASK           UINT8_C(0x01)

/** Mask definitions for INT_TAP register */
#define BMI160_TAP_DUR_MASK                     UINT8_C(0x07)
#define BMI160_TAP_SHOCK_DUR_MASK               UINT8_C(0x40)
#define BMI160_TAP_QUIET_DUR_MASK               UINT8_C(0x80)
#define BMI160_TAP_THRES_MASK                   UINT8_C(0x1F)

/** Mask definitions for INT_FLAT register */
#define BMI160_FLAT_THRES_MASK                  UINT8_C(0x3F)
#define BMI160_FLAT_HOLD_TIME_MASK              UINT8_C(0x30)
#define BMI160_FLAT_HYST_MASK                   UINT8_C(0x07)

/** Mask definitions for INT_LOWHIGH register */
#define BMI160_LOW_G_HYST_MASK                  UINT8_C(0x03)
#define BMI160_LOW_G_LOW_MODE_MASK              UINT8_C(0x04)
#define BMI160_HIGH_G_HYST_MASK                 UINT8_C(0xC0)

/** Mask definitions for INT_SIG_MOTION register */
#define BMI160_SIG_MOTION_SEL_MASK              UINT8_C(0x02)
#define BMI160_SIG_MOTION_SKIP_MASK             UINT8_C(0x0C)
#define BMI160_SIG_MOTION_PROOF_MASK            UINT8_C(0x30)

/** Mask definitions for INT_ORIENT register */
#define BMI160_ORIENT_MODE_MASK                 UINT8_C(0x03)
#define BMI160_ORIENT_BLOCK_MASK                UINT8_C(0x0C)
#define BMI160_ORIENT_HYST_MASK                 UINT8_C(0xF0)
#define BMI160_ORIENT_THETA_MASK                UINT8_C(0x3F)
#define BMI160_ORIENT_UD_ENABLE                 UINT8_C(0x40)
#define BMI160_AXES_EN_MASK                     UINT8_C(0x80)

/** Mask definitions for FIFO_CONFIG register */
#define BMI160_FIFO_GYRO      UINT8_C(0x80)
#define BMI160_FIFO_ACCEL     UINT8_C(0x40)
#define BMI160_FIFO_AUX       UINT8_C(0x20)
#define BMI160_FIFO_TAG_INT1      UINT8_C(0x08)
#define BMI160_FIFO_TAG_INT2      UINT8_C(0x04)
#define BMI160_FIFO_TIME      UINT8_C(0x02)
#define BMI160_FIFO_HEADER      UINT8_C(0x10)
#define BMI160_FIFO_CONFIG_1_MASK               UINT8_C(0xFE)
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

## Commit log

2024-10-20 adding CAD directory
2024-10-31 Delete CAD/maze overview_.f3z
    Extension error
    [maze overview_.f3z]
2024-11-07 Add files via upload
    Two wheels mouse
2024-11-07 Rename Mouse V3 v4.3mf to Mouse two wheels.3mf
    [Mouse two wheels.3mf]
2024-11-10 Programms to tests motors
2024-11-26 Completion of .h files for the exception of gyroscope (which has a dedicated library), utils and maze (taken care of by Félix)
2024-11-27 add motor.cpp, motion.cpp
2024-11-28 first version of motor library
2024-11-29 Gyroscope library
2024-11-30 first version of motor library finished
2024-12-02 test gyro BT
2024-12-02 implementation gyroscope calibration with tests
2024-12-02 make library for gyro
2024-12-02 test gyro with motors
2024-12-02 Printing walls according to an example maze
2024-12-03 corrections on gyroscope scripts
    [gyroscope.cpp]
2024-12-03 test for sensors
2024-12-03 adding a sensor api for the time of flight
2024-12-04 update the midle sensor
2024-12-04 remove synthax errors on sensors
    [sensors.cpp]
2024-12-04 add correction for forward
    [motion.cpp, motion.h]
2024-12-04 comment in gyroscope.cpp
2024-12-04 test turn with an angle with gyro
2024-12-05 Update README.md
    Tof calibration
2024-12-05 tuning the turns with gyro
2024-12-05 debugged + tested gyroscope
2024-12-06 Create assembly folder
2024-12-06 add of offset for gyro
2024-12-06 change functions in gyro to avoid deviation
    [gyroscope.cpp, motion.cpp, motors.h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]
2024-12-07 modifid turn and gyroscope
2024-12-07 renamed motor.cpp to motors.cpp
2024-12-08 added a way to correct a bit the direction
    [motion.cpp, motion.h]
2024-12-08 correction in test sensors
    [sensors_full.ino]
2024-12-09 added encoder Library
2024-12-09 block when main fails
    [main.cpp]
2024-12-10 first runs of maze debugging still some issues
    [first_maze_test.ino, navigation.cpp, sensors.cpp]
2024-12-11 removed some prints and fixed a core dump bug
    [first_maze_test.ino, navigation.cpp, sensors.cpp]
2024-12-11 added support for short mid sensos
    [first_maze_test.ino, navigation.cpp, sensors.cpp]
2024-12-11 mid sensor works now
2024-12-12 debuged navigation + changed speed + wheels ctes
2024-12-12 changed wheels
2024-12-13 changed wheels, tunning parameters
2024-12-17 images of esp32 screw on holder
2024-12-17 move images on assembly folder
2024-12-17 Added correction. (gyro + oriention) + debugged + lot of other things)
    [first_maze_test.ino, gyroscope.cpp, main.cpp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]
2024-12-17 image calibrations
2024-12-17 Adding use of button to switch to run mode
2024-12-17 Update README.md
    wiring diagram
2024-12-18 try init gyro ibefore run
2024-12-18 reset gyro before run
    [first_maze_test.ino, gyroscope.cpp]
2024-12-18 Add files via upload
    wiring diagrams
2024-12-26 Rename pillar 1cm.jpg to pillar_1cm.jpg
2024-12-26 Rename pillar 2cm.jpg to pillar_2cm.jpg
